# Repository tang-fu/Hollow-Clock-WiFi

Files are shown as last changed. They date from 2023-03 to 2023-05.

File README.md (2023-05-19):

# Hollow-Clock-WiFi

3D打印悬浮时钟  
> 声明
该项目原作者为[shiura](https://www.youtube.com/@shiura/about)创作的作品[Hollow-Clock-4](https://www.instructables.com/Hollow-Clock-4/)  
**本项目基于原作的 CC-BY-NC-SA 4.0 协议 在原项目基础上做出改进，不用做商业用途，仅供学习参考使用**
***
不得感叹原作本人的脑洞，原版的时钟是作为单机版本的装饰时钟，存有一定时间误差，且其底座结构窄，很难塞下主板以及驱动板，在此基础上，做了一些Cancel changes改进:  
- 加强其实用性，增添esp8266 nodemcu wifi模块，获取网络时间自主校时，第一次使用时需要误差校准，也可以通过模块内置网页调整时间
- 对其底座结构优化，能塞下wifi主板，驱动板
- 对其外壳增加时间刻度，便于查看时间
***
- 该项目没有整合led灯带，光污染的版本还在整理，后续开源，大家可以蹲一波  
- 该项目没有采用电池供电方案，因为电机功耗较大，18650锂电池大约维持50~80h
***
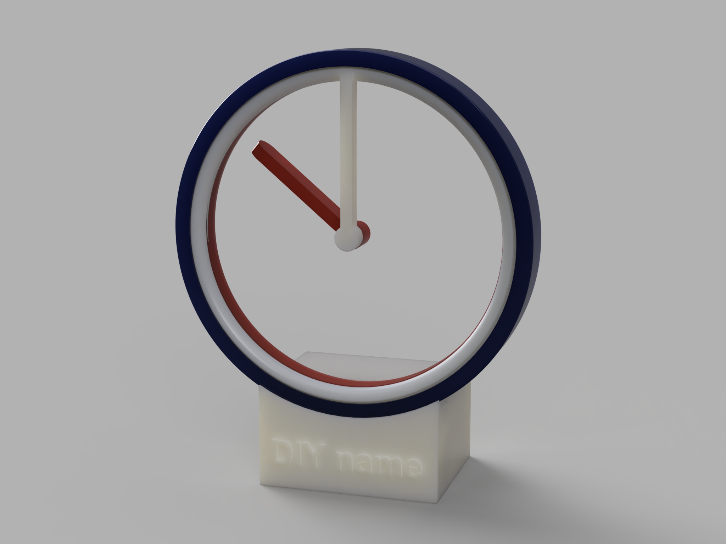
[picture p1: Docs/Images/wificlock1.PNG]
> 
***
## 项目文件说明

- 3D-model  
3d stl 模型文件
> 预览链接[点击传送]()暂时关闭
- Docs  
相关的耗材清单，参考文件，图片等

| 耗材名称 | 规格/型号 | 数量 | 其他 |
| --- | --- | --- | ---- |
| 铷磁铁 | 8x3mm | 3 | |
| 步进电机 | 28BYJ-48 | 1 | |
| 电机驱动板 | ULN2003 | 1 | 绿板 |
| 自攻螺丝 | M2(6mm,10mm) | 6mm:7,10mm:1 | 4mm可替代6mm |
| esp8266 | cp2102驱动 | 1 | 注意尺寸大小，有的板子过大，无法放入底座 |
| 线材 | \ | \ | |

- Codes  
该目录下为arduino程序，需要使用`Arduino IDE`运行  
——time_correction为误差校准程序  
——wifi_main_program为主程序，需要安装三个库文件  
`#include<ESP8266WiFi.h>`  
`#include<NTPClient.h>`  
`#include<WiFiUdp.h>`  
***
## 使用说明
1. 接线说明，程序中`int port[4] = { 15, 13, 12, 14 };`对应8266引脚如下图，分别对应ULN2003驱动板`IN1,IN2,IN3,IN4`，驱动板的电源与接地可以接到`Vin,GND`  
CP2102驱动下载官网:[https://www.silabs.com/interface/usb-bridges/classic/device.cp2102?tab=softwareandtools](https://www.silabs.com/interface/usb-bridges/classic/device.cp2102?tab=softwareandtools)

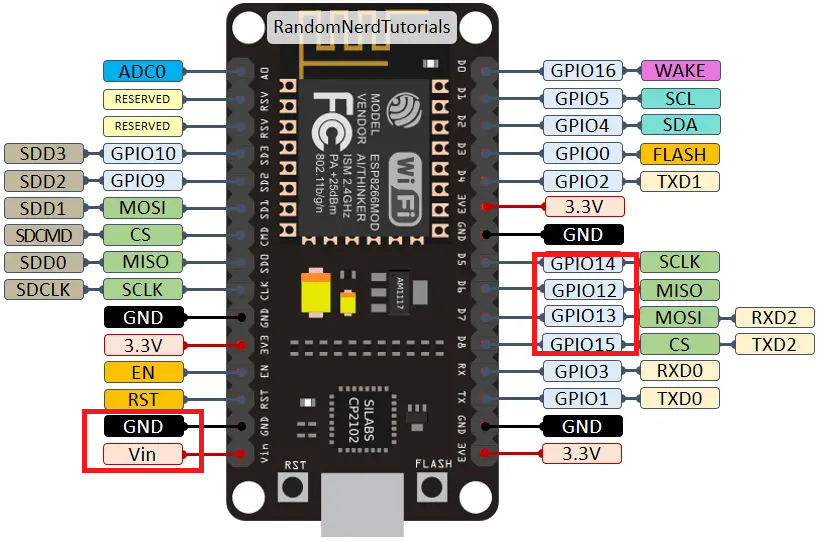
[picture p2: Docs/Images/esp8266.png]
> 

2. 第一次使用请先烧录该代码`time_corrections`，并将***分针和时针指向12点位置***，该程序会执行12次校准，（这个过程会持续10+分钟）最终回到12点位置，通过最后的误差角度，调整主程序代码中STEPS_PER_ROTATION的数值来进行校准`STEPS_PER_ROTATION = 30720 +- 偏差值`
3. 安装好库文件后，需要将主程序内的`INPUT_YOUR_WIFI_ID`，`INPUT_YOUR_WIFI_PASSWORD`修改为自己的WiFi名和密码，**将分针和时针指向12点位置**，烧录后重新上电，等待连接wifi，指针会自动走向当前时间
4. 如下图，分针时针均指向12点钟
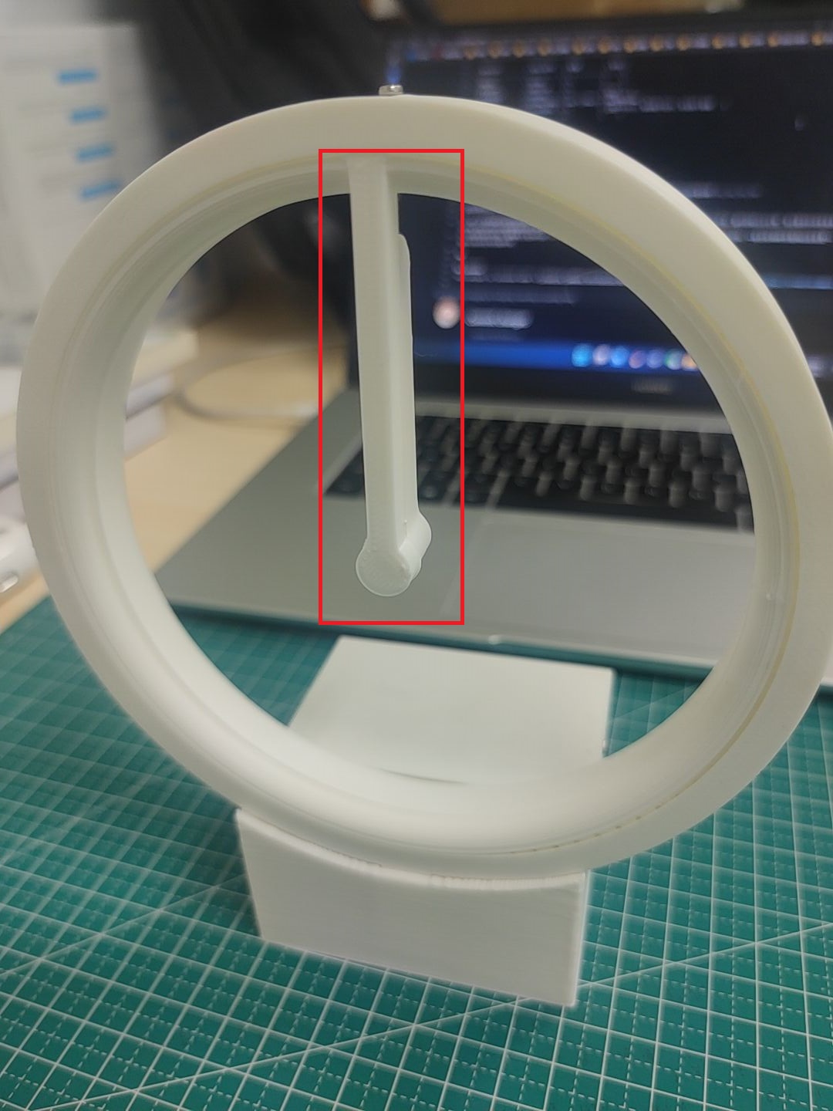
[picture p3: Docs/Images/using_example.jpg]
> 
5. [视频展示，校时教程](https://www.bilibili.com/video/BV1U24y1u7f5/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)
***
## 鸣谢
感谢[@shiura](https://www.youtube.com/@shiura/about)原作者提供的新奇创意  
感谢[@魔光堂_来一点光](https://space.bilibili.com/65500598)提供wifi自主校时的思路
***
## 赞助
如果你觉得这个项目对你有帮助，或者你有新的想法，欢迎你在此基础上继续创作  
并且情况允许的话，可以给我点一下star吗，总之非常感谢支持～
***
## License
This project is licensed under a [Creative Commons Attribution-NonCommercial-ShareAlike 4.0 International License](https://creativecommons.org/licenses/by-nc-sa/4.0/).

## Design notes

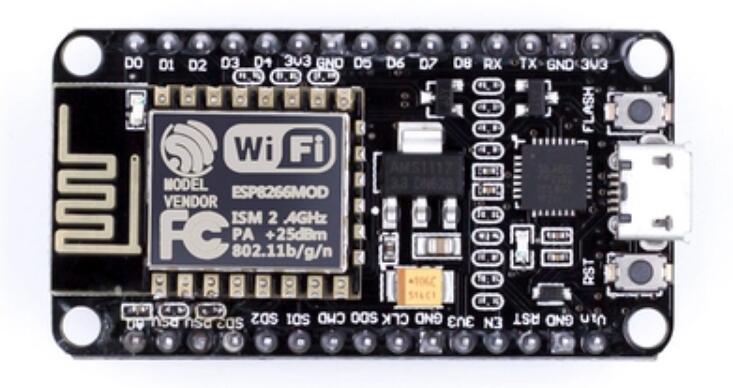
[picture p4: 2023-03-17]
Docs/Images/esp8266nodemcu.jpg

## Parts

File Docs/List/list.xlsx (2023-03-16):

序号 | 名称 | 规格/型号 | 数量 | 其他
1 | 铷磁铁 | 8x3mm | 3
2 | 步进电机 | 28BYJ-48 | 1
3 | 电机驱动板 | ULN2003 | 1 | 绿板
4 | 自攻螺丝 | M2 | (6mm:5，10mm:1)
5 | esp8266 | cp2102驱动 | 1 | 注意尺寸为下面图片这款
6 | 线材 | \ | \

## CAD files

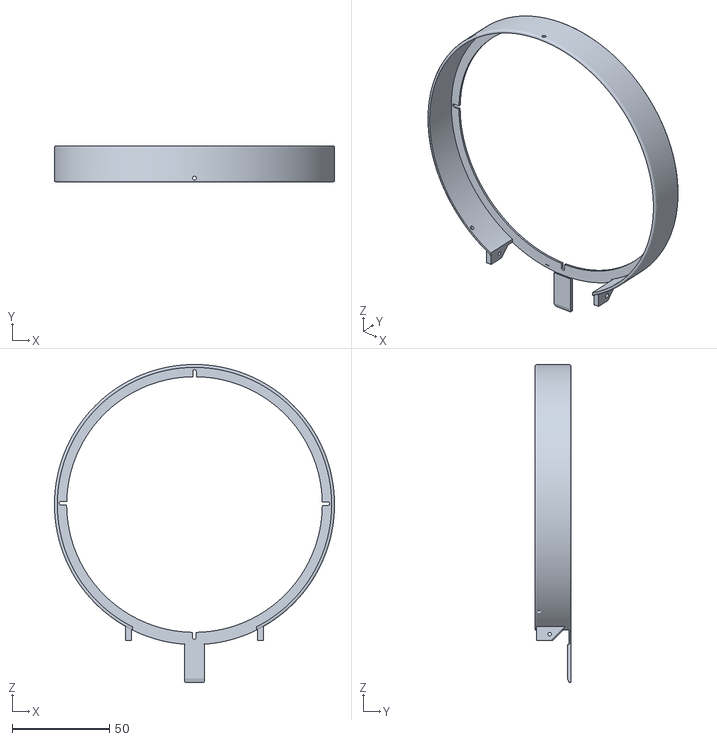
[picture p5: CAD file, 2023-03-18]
3D-Model/06转轴前盖.stl
144.0 x 18.5 x 163.5

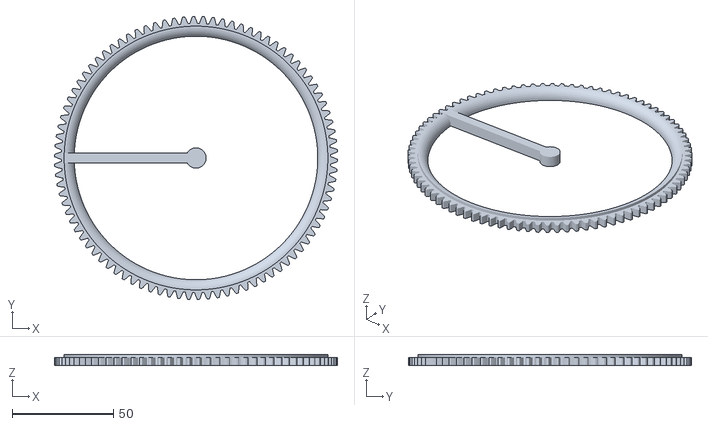
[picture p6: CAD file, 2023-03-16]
3D-Model/04分针转轴.stl
139.5 x 139.5 x 5.50

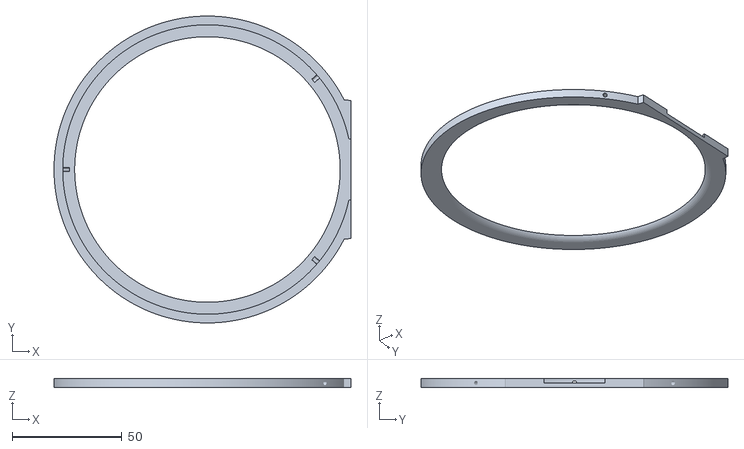
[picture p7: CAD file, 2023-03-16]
3D-Model/05转轴后盖.stl
135.5 x 140.0 x 4.00

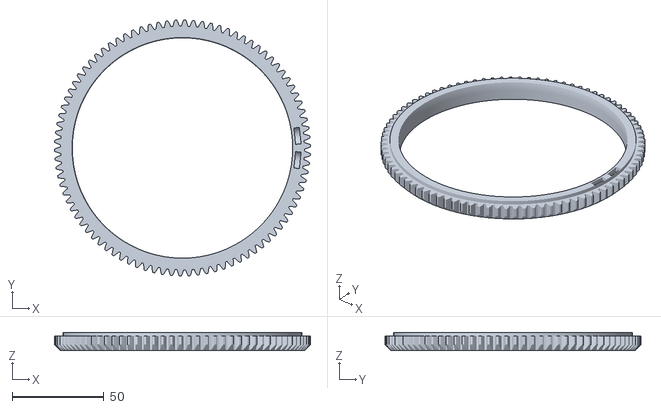
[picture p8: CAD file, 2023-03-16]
3D-Model/03时针转轴.stl
139.5 x 139.5 x 10.0

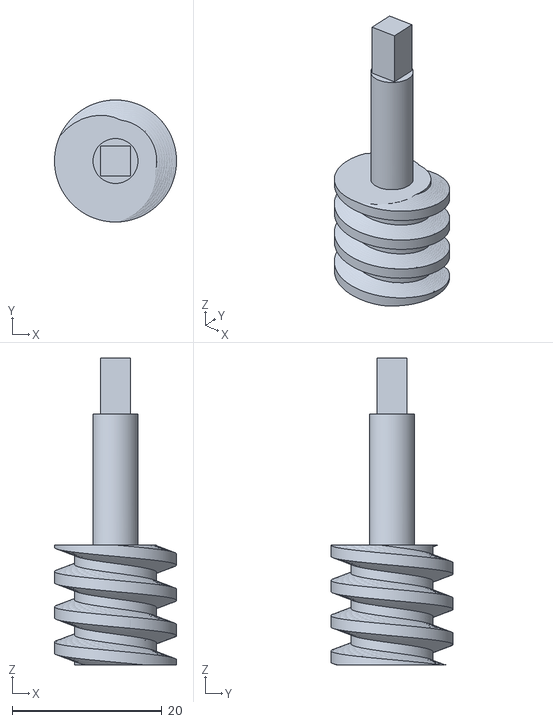
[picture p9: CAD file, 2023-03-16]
3D-Model/11旋转轴.stl
16.3 x 16.3 x 41.0

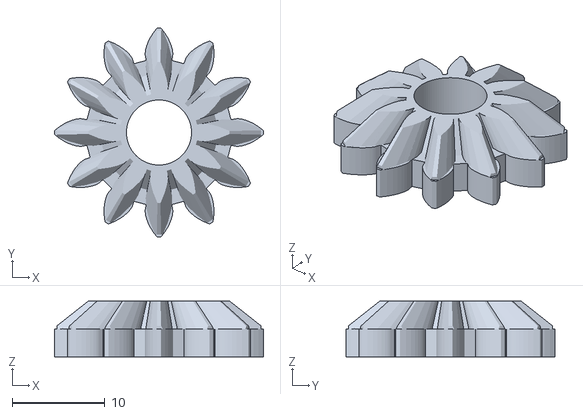
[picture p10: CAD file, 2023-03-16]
3D-Model/08大齿轮.stl
22.5 x 22.5 x 6.00

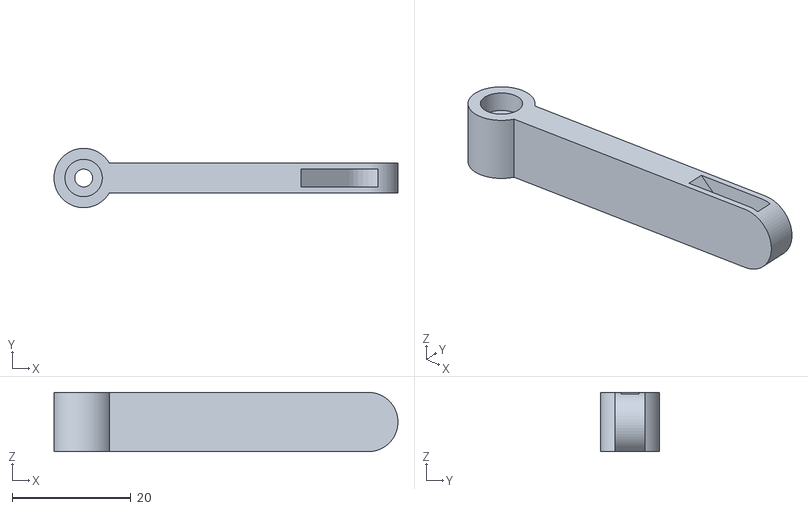
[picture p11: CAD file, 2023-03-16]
3D-Model/07时针指针.stl
58.0 x 10.0 x 10.0

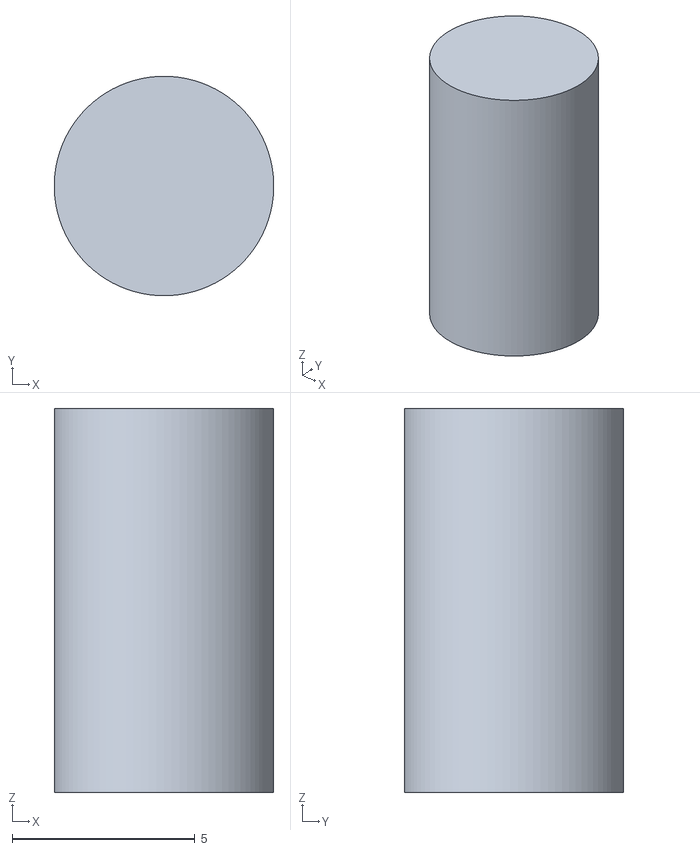
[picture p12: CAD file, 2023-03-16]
3D-Model/10圆柱轴.stl
6.00 x 6.00 x 10.5

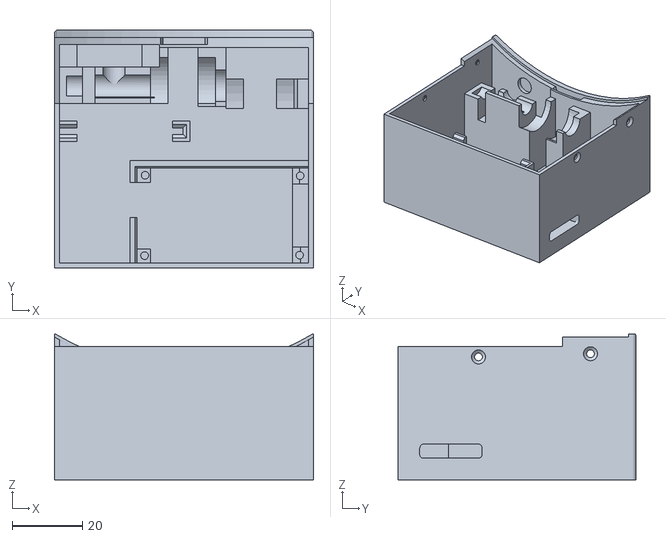
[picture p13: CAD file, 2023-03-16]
3D-Model/01wifi底座.stl
74.0 x 68.0 x 41.6

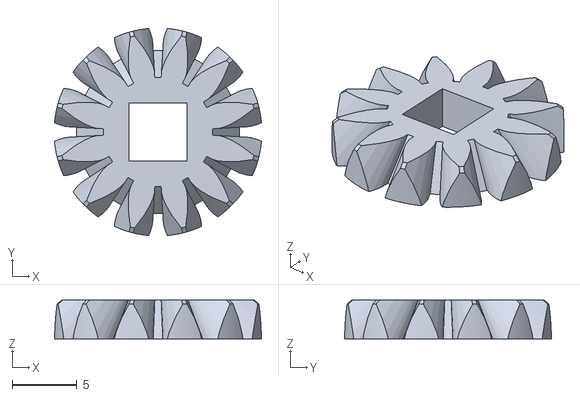
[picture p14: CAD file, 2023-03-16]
3D-Model/09小齿轮.stl
15.9 x 15.9 x 3.00

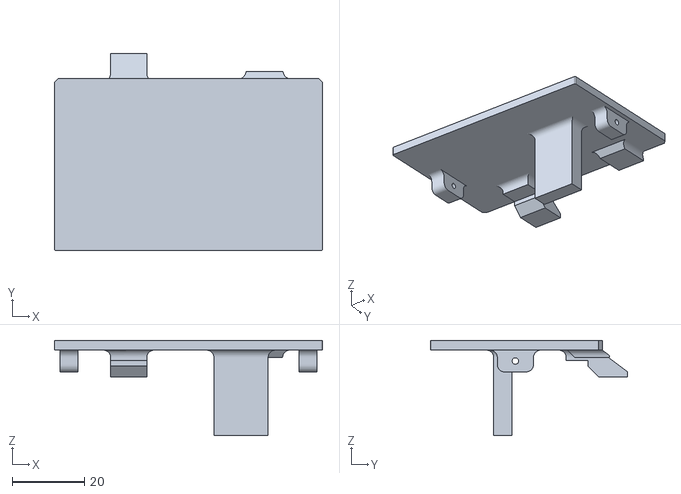
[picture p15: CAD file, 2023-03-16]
3D-Model/02wifi盖子.stl
74.0 x 54.5 x 26.3

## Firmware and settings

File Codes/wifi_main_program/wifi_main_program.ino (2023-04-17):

#include <NTPClient.h>
#include <ESP8266WiFi.h>
#include <WiFiUdp.h>
// 4096 * 90 / 12 = 30720 default
#define STEPS_PER_ROTATION 30743
const char *ssid = "Mi 11";
const char *password = "00000000";
int currentHour = 0;
int currentMinute = 0;
//int currentSeconds = 0;
WiFiUDP ntpUDP;
NTPClient timeClient(ntpUDP, "ntp1.aliyun.com", 60 * 60 * 8, 30 * 60 * 1000);  //偏移
int delaytime = 2;
int num = 0;
int port[4] = { 15, 13, 12, 14 };
// sequence of stepper motor control
int seq[8][4] = {
  { LOW, HIGH, HIGH, LOW },
  { LOW, LOW, HIGH, LOW },
  { LOW, LOW, HIGH, HIGH },
  { LOW, LOW, LOW, HIGH },
  { HIGH, LOW, LOW, HIGH },
  { HIGH, LOW, LOW, LOW },
  { HIGH, HIGH, LOW, LOW },
  { LOW, HIGH, LOW, LOW }
};

void setup() {
  Serial.begin(9600);
  WiFi_Begin();
  timeClient.begin();
  pinMode(port[0], OUTPUT);
  pinMode(port[1], OUTPUT);
  pinMode(port[2], OUTPUT);
  pinMode(port[3], OUTPUT);
  rotate(-20);  // for approach run
  rotate(20);   // approach run without heavy load
  for (num = 0; num < 50; num++) {
    timeClient.update();
    currentHour = timeClient.getHours();
    currentMinute = timeClient.getMinutes();
    Serial.print("当前时间:");
    Serial.print(currentHour);
    Serial.print(":");
    Serial.println(currentMinute);
  }
  Time_Correction(currentHour);
}

void loop() {
  static long prev_min = 0, prev_pos = 0, pos = 0;
  int min;
  min = Get_Current_Time();
  if (prev_min == min) {
    return;
  }
  prev_min = min;
  pos = (STEPS_PER_ROTATION * min) / 60;
  rotate(-20);  // for approach run
  rotate(20);   // approach run without heavy load
  if (pos - prev_pos > 0) {
    rotate(pos - prev_pos);
  }
  if (pos < prev_pos) {
    rotate(STEPS_PER_ROTATION / 60);
  }
  prev_pos = pos;
}

void WiFi_Begin() {
  WiFi.begin(ssid, password);
  while (WiFi.status() != WL_CONNECTED) {
    delay(500);
    Serial.print(".");
  }
  Serial.println("Wifi connected!");
}

int Get_Current_Time() {
  timeClient.update();
  //currentHour = timeClient.getHours();
  currentMinute = timeClient.getMinutes();
  //currentSeconds = timeClient.getSeconds();
  //Serial.println(currentMinute);//串口检查时间
  if (currentMinute == 0) {
    return 60;
  } else {
    return currentMinute;
  }
}

void rotate(int step) {
  static int phase = 0;
  int i, j, dt = 20;
  int delta = (step > 0) ? 1 : 7;

  step = (step > 0) ? step : -step;
  for (j = 0; j < step; j++) {
    phase = (phase + delta) % 8;
    for (i = 0; i < 4; i++) {
      digitalWrite(port[i], seq[phase][i]);
    }
    delay(dt);
    if (dt > delaytime) dt--;
  }
  // power cut
  for (i = 0; i < 4; i++) {
    digitalWrite(port[i], LOW);
  }
}

void Time_Correction(int hour) {
  int i;
  if (hour > 12) {
    hour -= 12;
  }
  Serial.print("当前小时:");
  Serial.println(hour);
  for (i = 1; i <= hour; i++) {
    int pos1 = 0, prev_pos1 = 0;
    pos1 = (STEPS_PER_ROTATION * 60) / 60;
    rotate(-20);  // for approach run
    rotate(20);   // approach run without heavy load
    if (pos1 - prev_pos1 > 0) {
      rotate(pos1 - prev_pos1);
    }
    Serial.print("第");
    Serial.print(i);
    Serial.println("圈结束");
  }
}

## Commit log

2023-03-16 添加图片
2023-03-16 stl文件
    [01wifi底座.stl, 02wifi盖子.stl, 03时针转轴.stl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]
2023-03-16 arduino代码
2023-03-17 自动校时程序
2023-03-17 3d前盖models
    [06转轴前盖.stl]
2023-03-17 展示图片
2023-03-17 增加照片
2023-03-18 电源引脚
2023-03-18 前盖模型修复
    [06转轴前盖.stl]
2023-04-17 Update wifi_main_program.ino
    修复每一小时后，第一分钟分针不转动的问题
